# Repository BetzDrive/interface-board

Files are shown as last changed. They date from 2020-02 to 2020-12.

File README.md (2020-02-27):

# Interface Board

This board is intended to connect a chain of 48 VDC RS-485 motor controllers to
the outside world.

## Features

 * USB - RS485 conversion. This is accomplished via the [FT232H](https://www.ftdichip.com/Products/ICs/FT232H.htm) and [ADM2682E](https://www.analog.com/en/products/adm2682e.html)
 IC's. The combination of these chips should provide full electrical isolation
 to the USB host and allow ~10 Mbps throughput to/from RS485.

 * Input power sanitizing. A [LM5066](https://www.ti.com/product/LM5066)
 hotswap controller IC provides sane controlled voltage ramps when the device
 is hot-plugged, and cuts power to the system when it exceeds ~56 volts. An
 input TVS diode starts kicks in around 65 V.

 * Backdrive surge supressing. Sometimes when motors are aggressively
 backdriven by an external power source, significant voltages are generated
 "back" onto the motor bus. The board is equipped to detect this condition and
 dump power through a 10-ohm power resistor. Hysteresis and timing is provided
 by a STM32L071 microcontroller.

## Resources

 * [Schematics in PDF](hardware/blue_interface_board.pdf)
 * KiCAD design files are found in [`hardware`](hardware)
 * fabrication files for rev.A are found in [`hardware/fab`](hardware/fab)

## Renderings

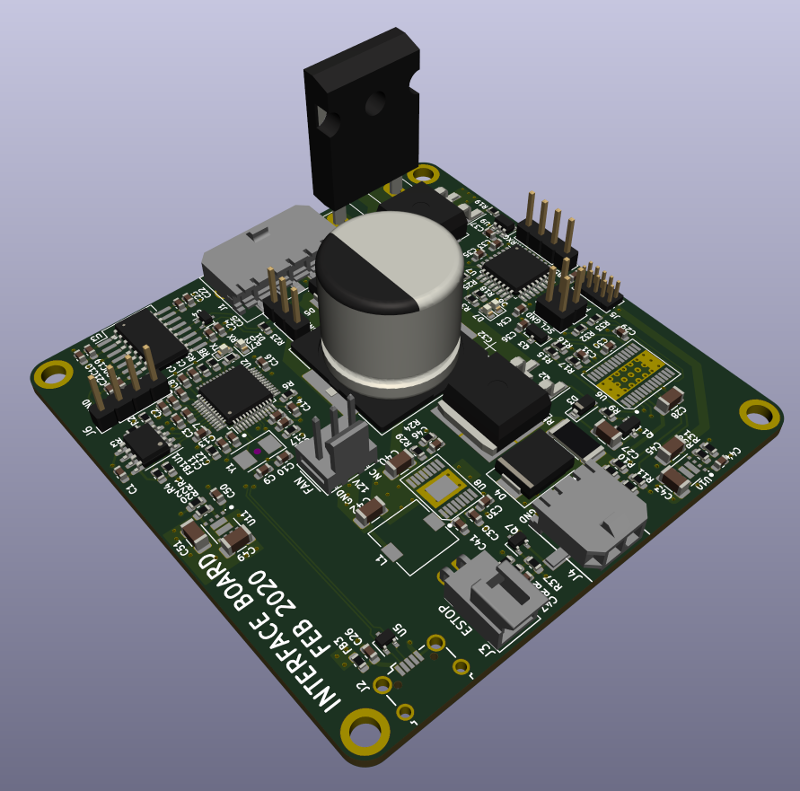
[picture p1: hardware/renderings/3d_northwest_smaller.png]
3d Northwest

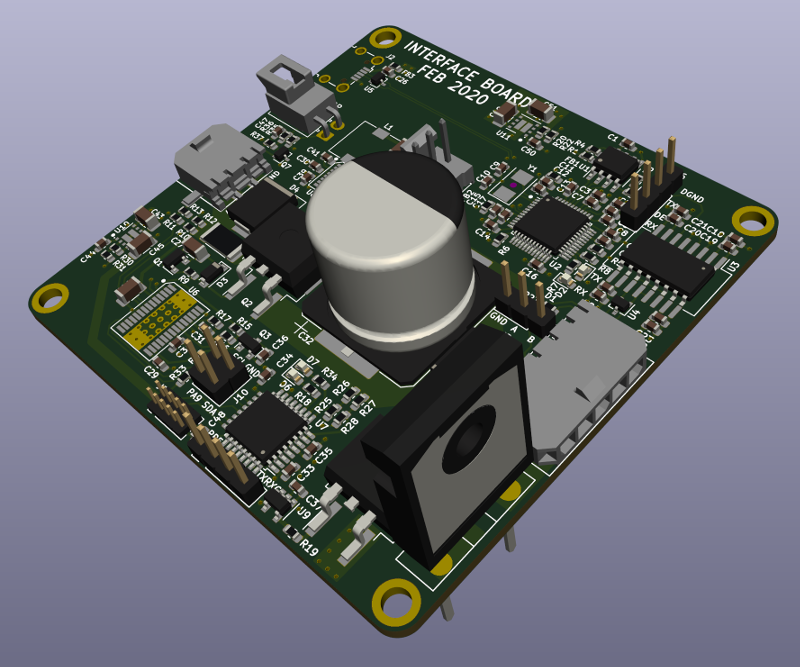
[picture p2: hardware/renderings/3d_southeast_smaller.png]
3d Southeast

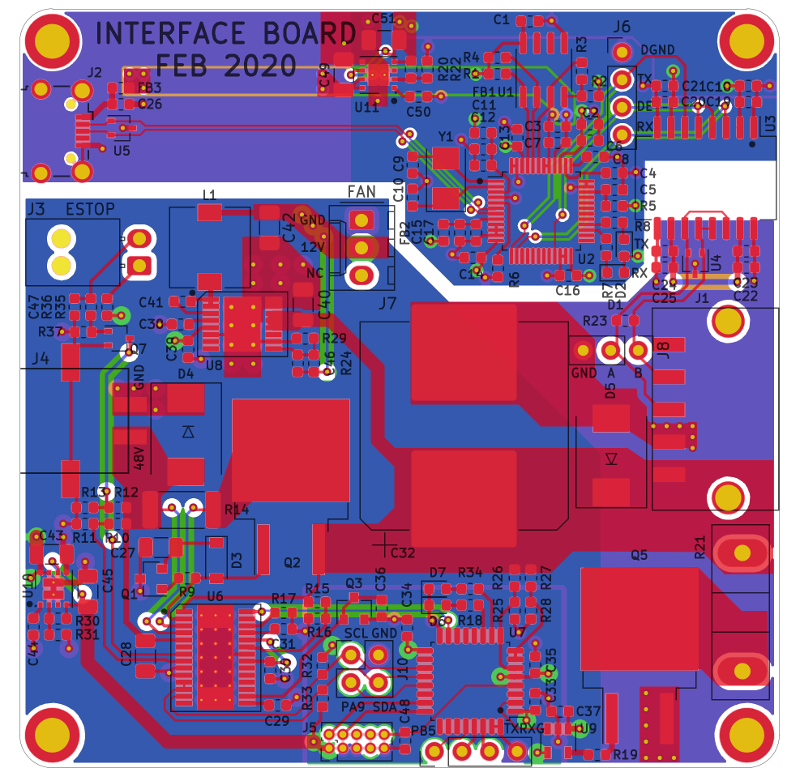
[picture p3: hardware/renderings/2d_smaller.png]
2d


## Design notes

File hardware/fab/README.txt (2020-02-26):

PCB fabrication notes
====
 * 4 layers
 * rectangular, 70mm x 70mm
 * 1.6mm finished thickness
 * green soldermask
 * white silkscreen
 * minimum via size 0.76mm (30mil), minimum via drill 0.38mm (15mil)
 * minimum trace/space 0.178mm (7mil)

Assembly notes:
====
 * SMT top side only. Minimum passives 0603.
 * two DFN regulator modules
 * otherwise, all legged IC packages: QFP, TSSOP, SOIC, etc.
 * please ignore all parts with "Do Not Populate" (DNP) part numbers
 * one through-hole power resistor (vertical TO-247 style)
 * three through-hole connectors
 * other through-hole connectors are DNP

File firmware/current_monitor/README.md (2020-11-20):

# compile it

```
git submodule init
git submodule update
sudo apt install gcc-arm-none-eabi
make
```

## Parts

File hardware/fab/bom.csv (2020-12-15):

Component | Quantity Per PCB | References | Value | Footprint | MFN | MPN | D1N | D1PN | Maximum Voltage | Tolerance
1 | 19 | C1 C4 C6 C7 C8 C12 C13 C14 C16 C17 C18 C20 C22 C24 C33 C34 C35 C47 C48 | 100n | C_0603_1608Metric | Yageo | CC0603KRX7R9BB104 | Digikey | 311-1344-1-ND
2 | 1 | C28 | 100nF | C_1206_3216Metric | AVX | 12061C104KAT2A | Digikey | 478-1529-1-ND | 100 V | 10%
3 | 4 | C5 C19 C23 C26 | 10n | C_0603_1608Metric | Yageo | CC0603KPX7R9BB103 | Digikey | 311-1572-1-ND
4 | 2 | C21 C25 | 10u | C_0603_1608Metric | Murata | GRM188R61A106KE69J | Digikey | 490-14372-1-ND
5 | 1 | C27 | 150nF | C_1206_3216Metric | KEMET | C1206C154KARACAUTO | Digikey | 399-17949-1-ND | 250 V | 10%
6 | 1 | C36 | 1n | C_0603_1608Metric | Yageo | CC0603KRX7R9BB102 | Digikey | 311-1080-1-ND
7 | 4 | C29 C30 C37 C39 | 1u | C_0603_1608Metric | Yageo | CC0603KRX5R8BB105 | Digikey | 311-1445-1-ND
8 | 3 | C42 C43 C49 | 22u | C_1206_3216Metric | Samsung | CL31A226KAHNNNE | Digikey | 1276-3047-1-ND | 25 V | 10%
9 | 2 | C9 C10 | 27p | C_0603_1608Metric | Yageo | CC0603JRNPO9BN270 | Digikey | 311-1063-1-ND
10 | 1 | C38 | 2u2 | C_0603_1608Metric | Yageo | CC0603KRX5R6BB225 | Digikey | 311-1451-1-ND | 10 V | 10%
11 | 4 | C2 C3 C11 C15 | 4.7u | C_0603_1608Metric | Tayio Yuden | LMK107BJ475KA-T | Digikey | 587-1441-1-ND | 10 V | 10%
12 | 1 | C41 | 470n | C_0603_1608Metric | Yageo | CC0603KRX5R8BB474 | Digikey | 311-3365-1-ND | 25 V | 10%
13 | 1 | C32 | 470u | CP_Elec_18x17.5 | Panasonic | EEE-FK1K471AM | Digikey | PCE4859CT-ND | 80 V | 20%
14 | 1 | C31 | 47n | C_0603_1608Metric | Samsung Electro-Mechanics | CL10B473JB8NNNC | Digikey | 1276-2070-2-ND
15 | 2 | C45 C51 | 47u | C_1206_3216Metric | Murata | GRM31CR61A476ME15L | Digikey | 490-5528-1-ND | 10 V | 10%
16 | 2 | C44 C50 | 4n7 | C_0603_1608Metric | Yageo | CC0603KRX7R0BB472 | Digikey | 311-3366-1-ND | 25 V | 10%
17 | 1 | C40 | 4u7 | C_1206_3216Metric | Murata | GRM31CC72A475KE11L | Digikey | 490-18620-1-ND | 100 V | 10%
18 | 1 | C46 | 82p | C_0603_1608Metric | Samsung | CL10C820JC81PNC | Digikey | 1276-2344-1-ND | 100 V | 5%
19 | 1 | D3 | 1N4148W-7-F | D_SOD-123 | Diodes Inc | 1N4148W-7-F | Digikey | 1N4148W-FDICT-ND
20 | 1 | D4 | 5.0SMDJ60A | D_SMC | Bourns | 5.0SMDJ60A | Digikey | 5.0SMDJ60ABBCT-ND
21 | 1 | D5 | B380-13-F | D_SMC | Diodes Inc | B380-13-F | Digikey | B380-FDICT-ND
22 | 2 | D1 D7 | GREEN | LED_0603_1608Metric | Wurth | 150060VS75000 | Digikey | 732-4980-1-ND
23 | 2 | D2 D6 | RED | LED_0603_1608Metric | Wurth | 150060RS75000 | Digikey | 732-4978-1-ND
24 | 3 | FB1 FB2 FB3 | 600R | R_0603_1608Metric | Wurth | 742792651 | Digikey | 732-1593-1-ND
25 | 1 | J5 | Conn_ARM_JTAG_SWD_10 | PinHeader_2x05_P1.27mm_Vertical | Sullins | GRPB052VWVN-RC | Digikey | S9015E-05-ND
26 | 1 | J3 | ESTOP | Molex_Nano-Fit_105313-xx02_1x02_P2.50mm_Horizontal | Molex | 1053131302 | Digikey | WM15141-ND
27 | 1 | J7 | FAN | Molex_KK-254_AE-6410-03A_1x03_P2.54mm_Vertical | Molex | 22232031 | Digikey | WM4201-ND
28 | 1 | J10 | I2C | PinHeader_2x02_P2.54mm_Vertical | DNP | DNP | DNP | DNP
29 | 1 | J4 | PWR | molex-0436500213 | Molex | 436500214 | Digikey | WM14310CT-ND
30 | 1 | J2 | USB_B_Micro | USB_Micro-B_Wuerth_629105150521_CircularHoles | Wurth | 629105150521 | Digikey | 732-5960-6-ND
31 | 1 | J1 | arm connector | molex-436500511 | Molex | 436500510 | Digikey | WM1888CT-ND
32 | 2 | J6 J9 | logic-side RS485 debug/expansion | PinHeader_1x04_P2.54mm_Vertical | DNP | DNP | DNP | DNP
33 | 1 | J8 | power-side RS485 debug/expansion | PinHeader_1x03_P2.54mm_Vertical | DNP | DNP | DNP | DNP
34 | 1 | L1 | 100u | L_7.3x7.3_H4.5 | Wurth | 744777920 | Digikey | 732-1199
35 | 1 | Q3 | MMBT3904 | SOT-23 | Diodes Inc | MMBT3904-7-F | Digikey | MMBT3904-FDICT-ND
36 | 1 | Q1 | MMBT5401LT1G | SOT-23 | ON Semi | MMBT5401LT1G | Digikey | MMBT5401LT1GOSCT-ND
37 | 1 | Q7 | NTS4001NT1G | SOT-323_SC-70 | ON Semi | NTS4001NT1G | Digikey | NTS4001NT1GOSTR-ND
38 | 2 | Q2 Q5 | PSMN4R8-100BSEJ | TO-263-2 | NXP | PSMN4R8-100BSEJ | Digikey | 1727-1103-1-ND
39 | 1 | R37 | 100k | R_0603_1608Metric | Yageo | RC0603FR-07100KL | Digikey | 311-100KHRCT-ND |  | 1%
40 | 5 | R1 R2 R4 R5 R36 | 10K | R_0603_1608Metric | Yageo | RC0603JR-0710KL | Digikey | 311-10KGRCT-ND
41 | 1 | R21 | 10R | TO-247-2_Vertical | Riedon | PF2472-10RF1 | Digikey | 696-1107-5-ND
42 | 1 | R23 | 120 | R_0603_1608Metric | Yageo | RC0603FR-07120RL | Digikey | 311-120HRCT-ND |  | 1%
43 | 1 | R6 | 12K | R_0603_1608Metric | Panasonic | ERA-3AEB123V | Digikey | P12KDBCT-ND |  | 0.1%
44 | 1 | R16 | 13.3k | R_0603_1608Metric | Panasonic | ERA-3AEB1332V | Digikey | P13.3KDBTR-ND |  | 0.1%
45 | 6 | R10 R12 R22 R26 R27 R31 | 140k | R_0603_1608Metric | Panasonic | ERA-3AEB1403V | Digikey | P140KDBCT-ND |  | 0.1%
46 | 1 | R24 | 1M | R_0603_1608Metric | Yageo | RC0603FR-071ML | Digikey | 311-1.00MHRCT-ND |  | 1%
47 | 2 | R9 R35 | 1k | R_0603_1608Metric | Yageo | RC0603FR-071KL | Digikey | 311-1.00KHRCT-ND |  | 1%
48 | 3 | R3 R32 R33 | 2.2k | R_0603_1608Metric | Yageo | RC0603FR-072K2L | Digikey | 311-2.20KHRCT-ND |  | 1%
49 | 1 | R15 | 240k | R_0603_1608Metric | Panasonic | ERA-3AEB244V | Digikey | P240KDBTR-ND |  | 0.1%
50 | 1 | R13 | 25k5 | R_0603_1608Metric | Panasonic | ERA-3AEB2552V | Digikey | P25.5KDBCT-ND |  | 0.1%
51 | 1 | R17 | 300k | R_0603_1608Metric | Panasonic | ERA-3AEB304V | Digikey | P300KDBTR-ND |  | 0.1%
52 | 1 | R19 | 33 | R_0603_1608Metric | Yageo | RC0603FR-0733RL | Digikey | 311-33.0HRCT-ND |  | 1%
53 | 2 | R20 R30 | 437k | R_0603_1608Metric | Yageo | RC0603FR-07432KL | Digikey | 311-432KHRCT-ND |  | 1%
54 | 4 | R7 R8 R18 R34 | 470R | R_0603_1608Metric | Yageo | RC0603FR-07470RL | Digikey | 311-470HRCT-ND |  | 1%
55 | 1 | R14 | 4m | R_2512_6332Metric | Vishay Dale | WSL25124L000FEA18 | Digikey | WSLH-.004TR-ND
56 | 1 | R28 | 6.34k | R_0603_1608Metric | Panasonic | ERA-3AEB6341V | Digikey | P6.34KDBCT-ND |  | 0.1%
57 | 1 | R25 | 6.65k | R_0603_1608Metric | Panasonic | ERA-3AEB6651V | Digikey | P6.65KDBCT-ND |  | 0.1%
58 | 1 | R11 | 6k49 | R_0603_1608Metric | Panasonic | ERA-3AEB6491V | Digikey | P6.49KDBCT-ND |  | 0.1%
59 | 1 | R29 | 91k | R_0603_1608Metric | Yageo | RC0603FR-0791KL | Digikey | 311-91.0KHRDKR-ND |  | 1%
60 | 1 | U1 | 93LCxxB | SOIC-8_3.9x4.9mm_P1.27mm | Microchip | 93LC56B/SN | Digikey | 93LC56B/SN-ND
61 | 1 | U3 | ADM2682E | SOIC-16W_7.5x12.8mm_P1.27mm | Analog Devices | ADM2682EBRIZ | Digikey | ADM2682EBRIZ-ND
62 | 1 | U9 | FAN3111E | SOT-23-5 | ON Semi | FAN3111ESX | Digikey | FAN3111ESXCT-ND
63 | 1 | U2 | FT232H | LQFP-48_7x7mm_P0.5mm | FTDI | FT232HL-REEL | Digikey | 768-1101-1-ND
64 | 1 | U8 | LM46000 | PWP0016G | TI | LM46000PWPR | Digikey | 296-40222-1-ND
65 | 1 | U6 | LM5066 | Texas_PWP0028A | TI | LM5066PMHX/NOPB | Digikey | 296-LM5066PMHX/NOPBCT-ND
66 | 2 | U10 U11 | LMZ21700SIL | SIL0008E | TI | LMZ21700SILR | Digikey | 296-44325-1-ND
67 | 1 | U7 | STM32L071KZT6 | LQFP-32_7x7mm_P0.8mm | ST | STM32L071KZT6 | Digikey | 497-18578-ND
68 | 2 | U4 U5 | TPD2E2U06DCK | SOT-323_SC-70 | TI | TPD2E2U06DCKR | Digikey | 296-TPD2E2U06DCKRDKR-ND
69 | 1 | Y1 | 12MHz | Crystal_SMD_5032-2Pin_5.0x3.2mm | Kyocera | CX5032GB12000H0HPQZ1 | Digikey | 1253-1375-1-ND
Component Groups: | 69
Component Count: | 126
Fitted Components: | 126
Number of PCBs: | 1
Total components: | 126
Schematic Version:
Schematic Date:
PCB Variant: | ['default']
BoM Date: | Mon 14 Dec 2020 11:55:06 PM PST
Schematic Source: | blue_interface_board.kicad_sch
KiCad Version: | Eeschema 5.99.0-unknown-dd374e12a~102~ubuntu20.04.1

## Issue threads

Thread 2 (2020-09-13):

Firmware for Reverse Current Circuitry

gbalke, 2020-09-13:
A small driver needs to be written to toggle the shunt (R21) in case of regeneration caused by backdrive of the motor controllers. For now, R21 is to be left unpopulated.

gbalke, 2020-11-11:
Initial steps addressed by #4.

gbalke, 2020-11-19:
Currently debugging upload issues on this [branch](https://github.com/BetzDrive/interface-board/tree/upload_debug) with firmware [here](https://github.com/BetzDrive/interface-board/tree/upload_debug/firmware/current_monitor).

When I upload and attach a debugger I get the following:
```
Reading symbols from build/program.elf...
Remote debugging using localhost:3333
0xbc08bcf8 in ?? ()
(gdb) b *main
Breakpoint 1 at 0x8130: file src/main.c, line 18.
(gdb) start
The program being debugged has been started already.
Start it from the beginning? (y or n) y
Temporary breakpoint 2 at 0x8134: file src/main.c, line 21.
Starting program: ......./project/build/program.elf
Note: automatically using hardware breakpoints for read-only addresses.
^C
Program received signal SIGTRAP, Trace/breakpoint trap.
0xfffffffe in ?? ()
(gdb)
```

Probing shows everything is working alright...
```
$ st-info --probe
Found 1 stlink programmers
 serial: 303030303030303030303031
openocd: "\x30\x30\x30\x30\x30\x30\x30\x30\x30\x30\x30\x31"
  flash: 196608 (pagesize: 128)
   sram: 20480
 chipid: 0x0447
  descr: L0x Category 5 device
```

My openocd upload is definitely complaining but not failing and I've had similar results using st-flash:
```
Info : Device: STM32L0xx (Cat.5)
Info : STM32L flash has dual banks. Bank (0) size is 128kb, base address is 0x8000000
flash 'stm32lx' found at 0x08000000
auto erase enabled
Warn : couldn't use loader, falling back to page memory writes
wrote 8192 bytes from file build/program.bin in 1.138968s (7.024 KiB/s)
Error: JTAG failure
Error: Error setting register
Error: timed out while waiting for target halted
target halted due to debug-request, current mode: Handler HardFault
xPSR: 0xf0000003 pc: 0xfffffffe msp: 0x46c0b5f8
Error: error executing cortex_m crc algorithm
verified 6784 bytes in 20.159586s (0.329 KiB/s)
adapter speed: 300 kHz
shutdown command invoked
```

The crc error comes and goes...

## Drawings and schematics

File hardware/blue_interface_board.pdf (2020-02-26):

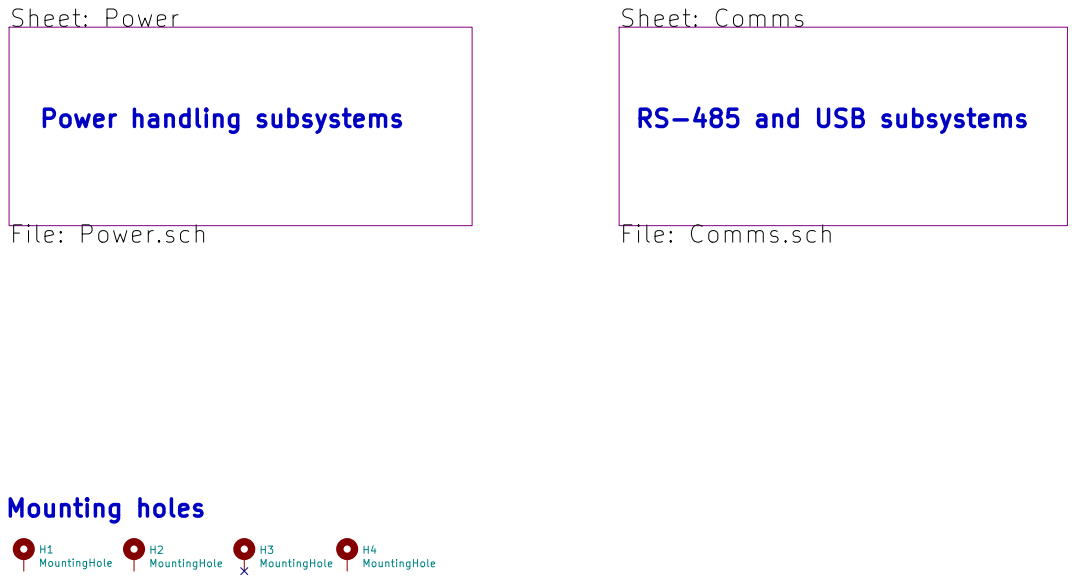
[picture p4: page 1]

File: blue_interface_board.sch Sheet: / Sheet: Comms

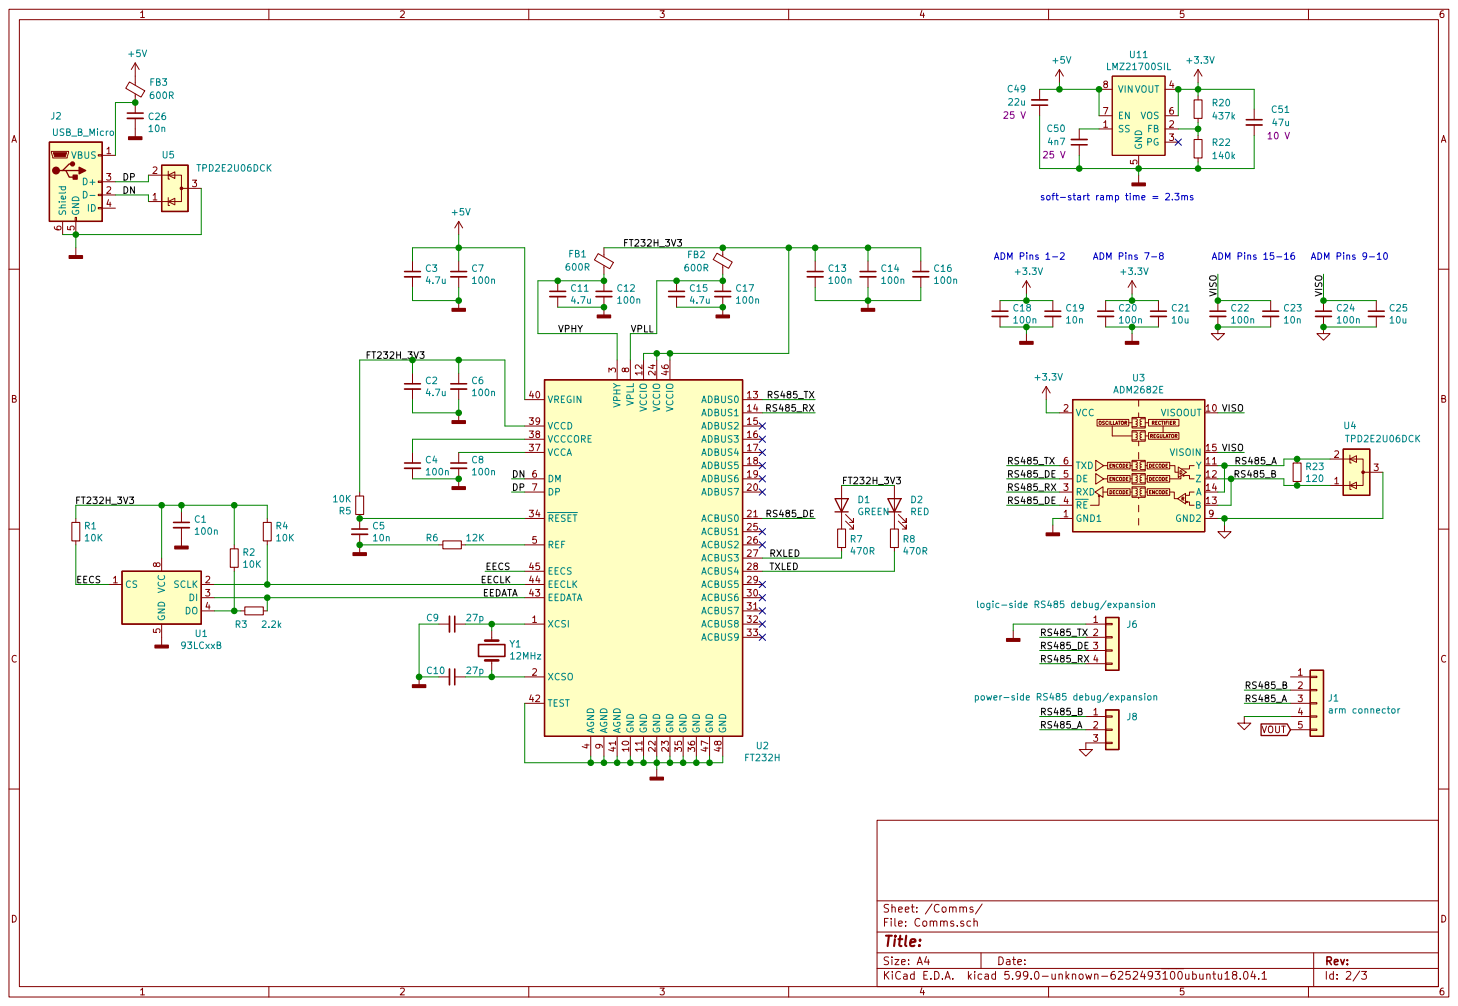
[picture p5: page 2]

5 VOS 6 EN 7 VIN 8 SS 1 U11

soft-start ramp time = 2.3ms

4 VREGIN 40 AGND 41 TEST 42 EEDATA 43 EECLK 44 EECS 45 VCCIO 46 GND 47 GND 48 REF 5 DM 6 DP 7 VPLL

3 ACBUS6 30 ACBUS7 31 ACBUS8 32 ACBUS9 33 RESET 34 GND 35 GND 36 VCCA 37 VCCCORE 38 VCCD 39 AGND

Id: 2/3 Title: File: Comms.sch Sheet: /Comms/ R5

power-side RS485 debug/expansion

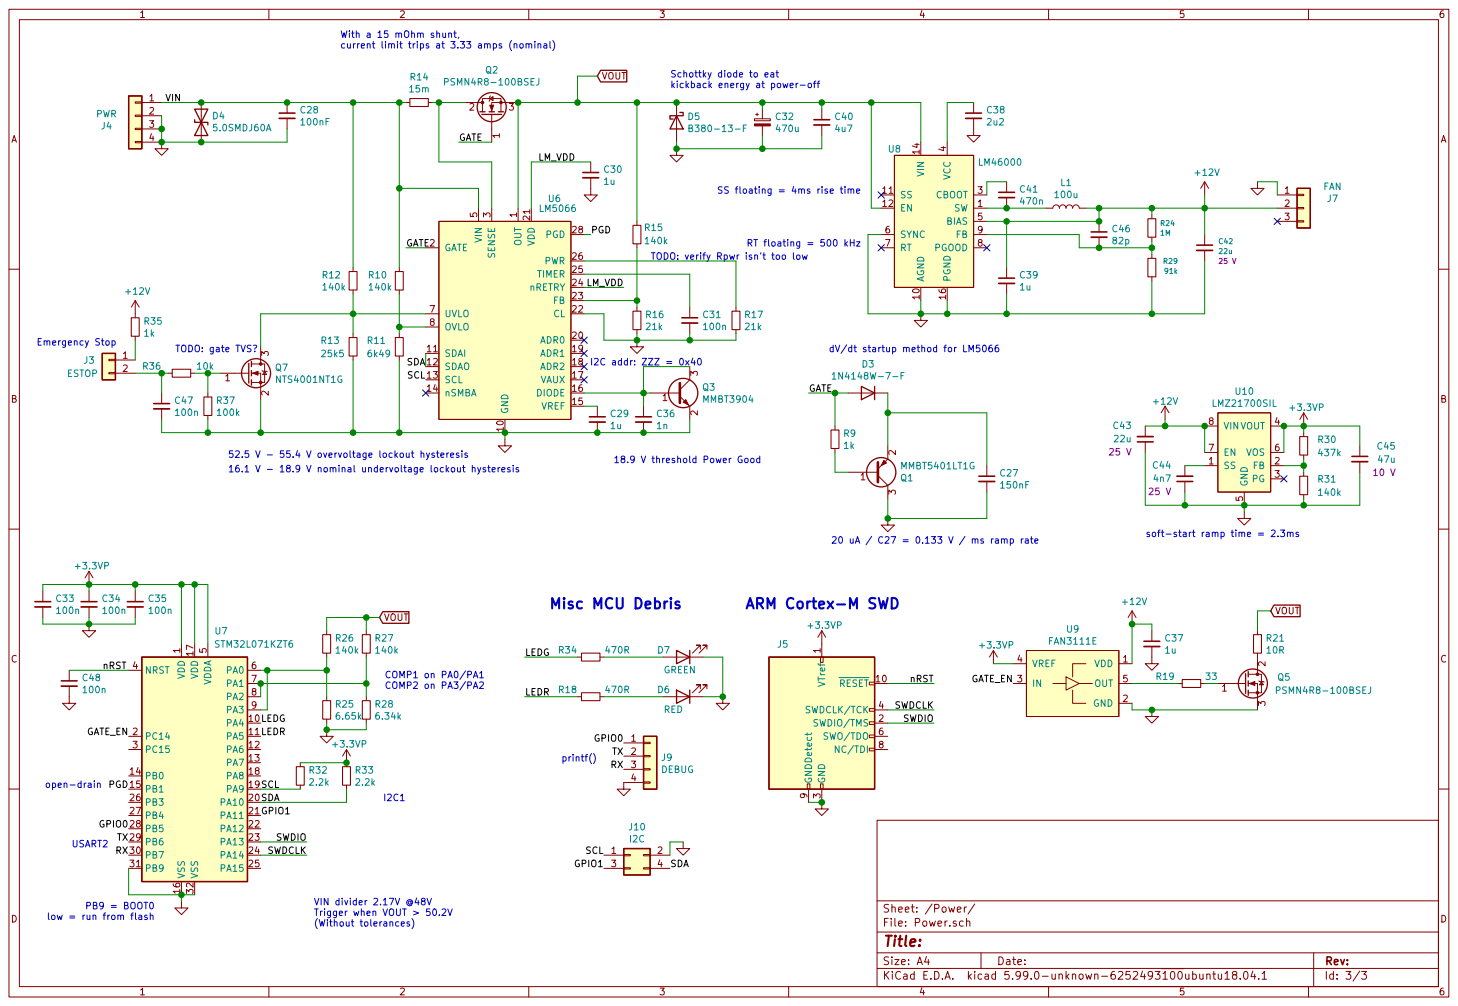
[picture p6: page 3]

With a 15 mOhm shunt, current limit trips at 3.33 amps (nominal)
VOUT VOUT SWDCLK

Schottky diode to eat
kickback energy at power-off

4 BIAS 5 SYNC 6 RT 7 PGOOD 8 FB 9 U8

SS floating = 4ms rise time

1 GND 10 SDAI 11 SDAO 12 SCL 13
GATE

TODO: verify Rpwr isn't too low

5 VOS 6 EN 7 VIN 8 SS 1 U10
LMZ21700SIL

18.9 V threshold Power Good VIN divider 2.17V @48V

2 3 Q1MMBT5401LT1G VTref 1 RESET 10 SWDIO/TMS 2 GND

16.1 V - 18.9 V nominal undervoltage lockout hysteresis

20 uA / C27 = 0.133 V / ms ramp rate COMP1 on PA0/PA1 COMP2 on PA3/PA2

soft-start ramp time = 2.3ms

3 SWDCLK/TCK 4 SWO/TDO 6 NC/TDI 8 GNDDetect 9

low = run from flash

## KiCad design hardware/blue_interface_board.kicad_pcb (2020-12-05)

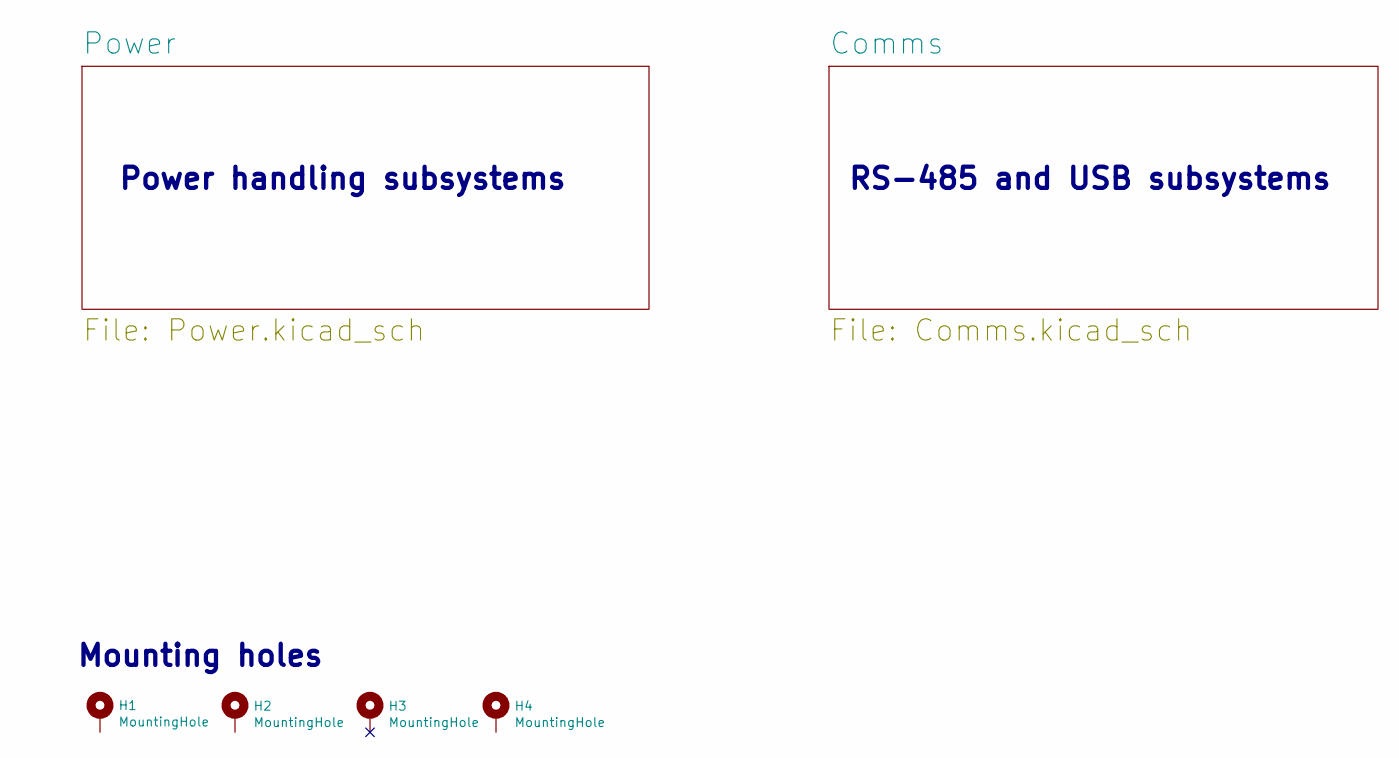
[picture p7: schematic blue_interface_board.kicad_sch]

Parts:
H1, H2, H3, H4: MountingHole; MountingHole_3.2mm_M3_DIN965_Pad

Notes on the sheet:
Mounting holes
Power handling subsystems
RS-485 and USB subsystems

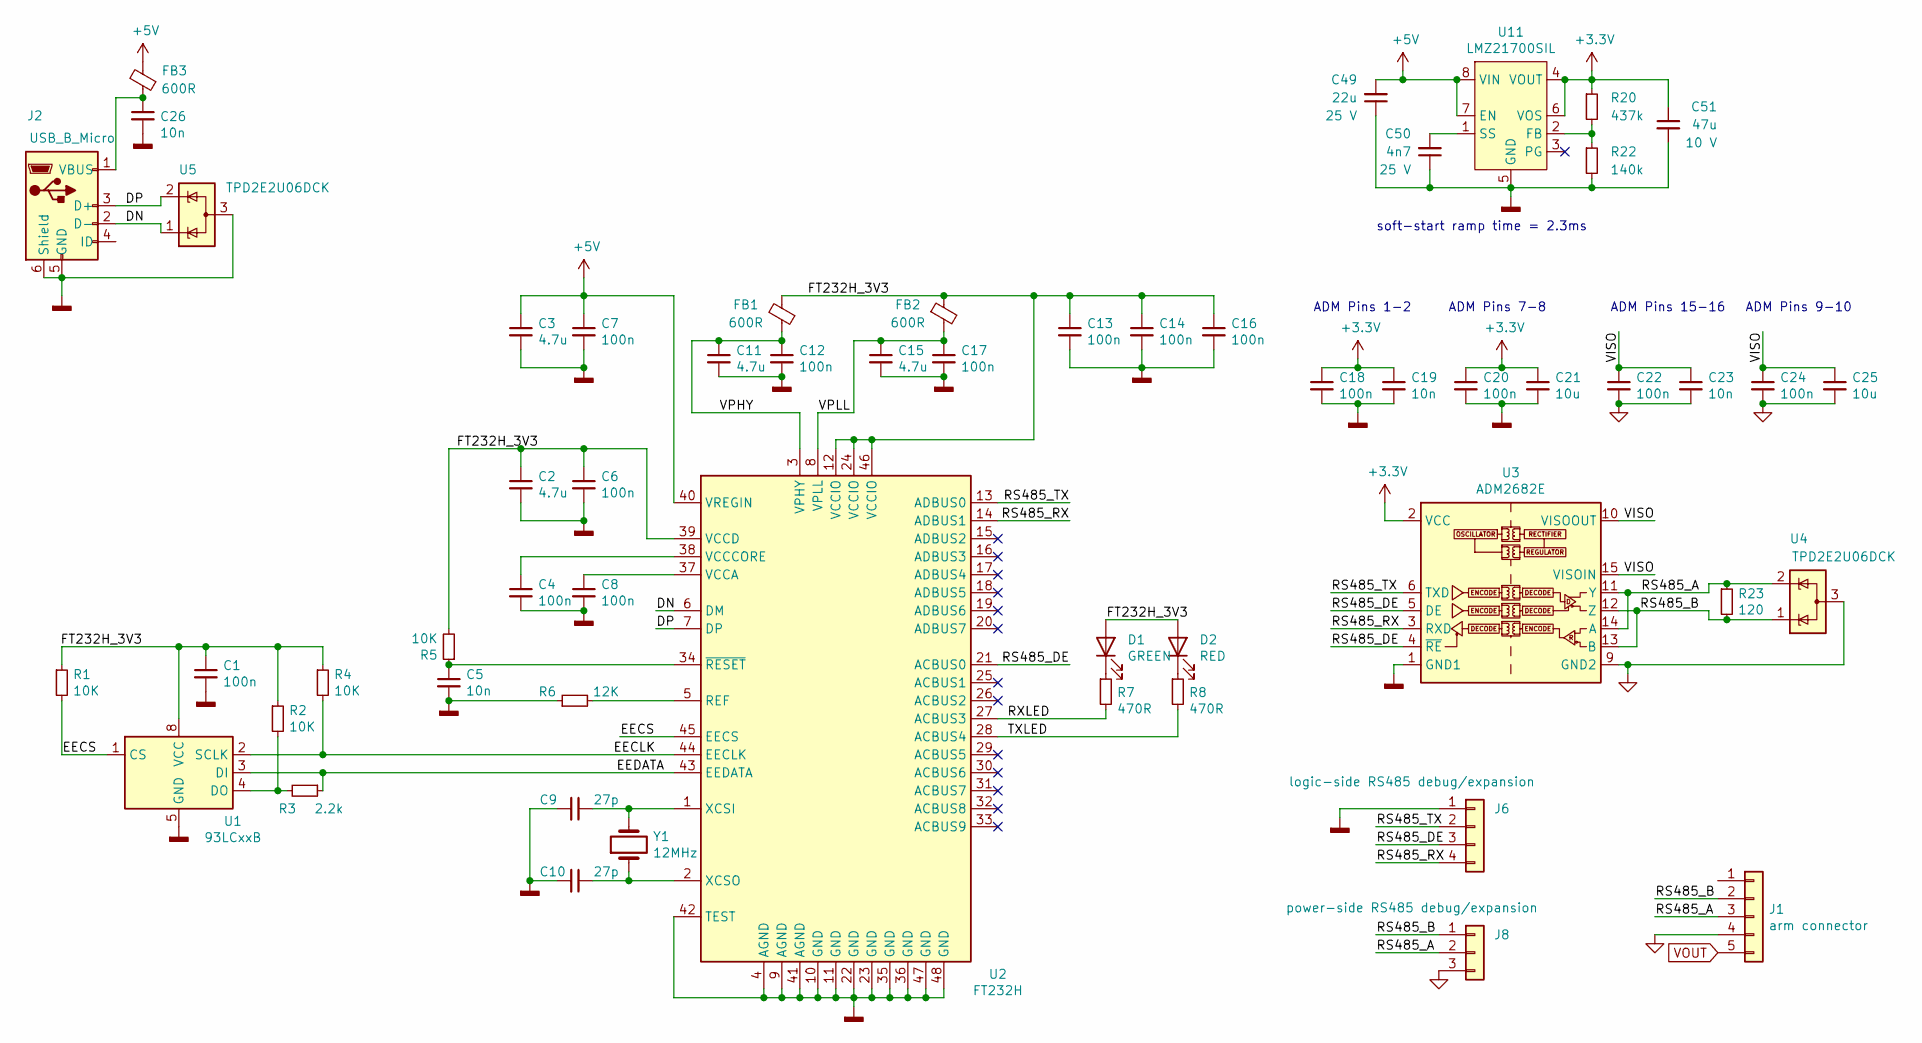
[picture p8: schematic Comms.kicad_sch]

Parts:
C1, C4, C6, C7, C8, C12, C13, C14, C16, C17, C18, C20, C22, C24: 100n; C_0603_1608Metric; MPN CC0603KRX7R9BB104
C2, C3, C11, C15: 4.7u; C_0603_1608Metric; Maximum Voltage 10 V; Tolerance 10%; MPN LMK107BJ475KA-T
C5, C19, C23, C26: 10n; C_0603_1608Metric; MPN CC0603KPX7R9BB103
C9, C10: 27p; C_0603_1608Metric; MPN CC0603JRNPO9BN270
C21, C25: 10u; C_0603_1608Metric; MPN GRM188R61A106KE69J
C49: 22u; C_1206_3216Metric; Maximum Voltage 25 V; Tolerance 10%; MPN CL31A226KAHNNNE
C50: 4n7; C_0603_1608Metric; Maximum Voltage 25 V; Tolerance 10%; MPN CC0603KRX7R0BB472
C51: 47u; C_1206_3216Metric; Maximum Voltage 10 V; Tolerance 10%; MPN GRM31CR61A476ME15L
D1: GREEN; LED_0603_1608Metric; MPN 150060VS75000
D2: RED; LED_0603_1608Metric; MPN 150060RS75000
FB1, FB2, FB3: 600R; R_0603_1608Metric; MPN 742792651
J1: arm connector; molex-436500511; MPN 436500510
J2: USB_B_Micro; USB_Micro-B_Wuerth_629105150521_CircularHoles; MPN 629105150521
J6: logic-side RS485 debug/expansion; PinHeader_1x04_P2.54mm_Vertical; MPN DNP
J8: power-side RS485 debug/expansion; PinHeader_1x03_P2.54mm_Vertical; MPN DNP
R1, R2, R4, R5: 10K; R_0603_1608Metric; MPN RC0603JR-0710KL
R3: 2.2k; R_0603_1608Metric; Tolerance 1%; MPN RC0603FR-072K2L
R6: 12K; R_0603_1608Metric; Tolerance 0.1%; MPN ERA-3AEB123V
R7, R8: 470R; R_0603_1608Metric; Tolerance 1%; MPN RC0603FR-07470RL
R20: 437k; R_0603_1608Metric; Tolerance 1%; MPN RC0603FR-07432KL
R22: 140k; R_0603_1608Metric; Tolerance 0.1%; MPN ERA-3AEB1403V
R23: 120; R_0603_1608Metric; Tolerance 1%; MPN RC0603FR-07120RL
U1: 93LCxxB; SOIC-8_3.9x4.9mm_P1.27mm; MPN 93LC56B/SN
U2: FT232H; LQFP-48_7x7mm_P0.5mm; MPN FT232HL-REEL
U3: ADM2682E; SOIC-16W_7.5x12.8mm_P1.27mm; MPN ADM2682EBRIZ
U4, U5: TPD2E2U06DCK; SOT-323_SC-70; MPN TPD2E2U06DCKR
U11: LMZ21700SIL; SIL0008E; MPN LMZ21700SILR
Y1: 12MHz; Crystal_SMD_5032-2Pin_5.0x3.2mm; MPN CX5032GB12000H0HPQZ1

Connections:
+3V3: C18.1, C19.1, C20.1, C21.1, C51.1, R20.1, U3.2 (VCC), U3.7 (VCC), U11.4 (VOUT), U11.6 (VOS)
+5V: C3.1, C7.1, C49.2, FB3.2, U2.40 (VREGIN), U11.7 (EN), U11.8 (VIN)
/Comms/DN: J2.2 (D-), U2.6 (DM), U5.1 (K)
/Comms/DP: J2.3 (D+), U2.7 (DP), U5.2 (K)
/Comms/EECLK: R4.2, U1.2 (SCLK), U2.44 (EECLK)
/Comms/EECS: R1.2, U1.1 (CS), U2.45 (EECS)
/Comms/EEDATA: R3.1, U1.3 (DI), U2.43 (EEDATA)
/Comms/FT232H_3V3: C1.1, C2.1, C6.1, C13.1, C14.1, C16.1, D1.2 (A), D2.2 (A), FB1.2, FB2.1, R1.1, R2.1, R4.1, R5.2, U1.8 (VCC), U2.12 (VCCIO), U2.24 (VCCIO), U2.39 (VCCD), U2.46 (VCCIO)
/Comms/RS485_A: J1.3, J8.2, R23.1, U3.11 (Y), U3.14 (A), U4.2 (K)
/Comms/RS485_B: J1.2, J8.1, R23.2, U3.12 (Z), U3.13 (B), U4.1 (K)
/Comms/RS485_DE: J6.3, U2.21 (ACBUS0), U3.4 (~RE), U3.5 (DE)
/Comms/RS485_RX: J6.4, U2.14 (ADBUS1), U3.3 (RXD)
/Comms/RS485_TX: J6.2, U2.13 (ADBUS0), U3.6 (TXD)
/Comms/RXLED: R7.2, U2.27 (ACBUS3)
/Comms/TXLED: R8.2, U2.28 (ACBUS4)
/Comms/VISO: C22.1, C23.1, C24.1, C25.1, U3.10 (VISOOUT), U3.15 (VISOIN)
/Comms/VPHY: C11.1, C12.1, FB1.1, U2.3 (VPHY)
/Comms/VPLL: C15.1, C17.1, FB2.2, U2.8 (VPLL)
GND: C22.2, C23.2, C24.2, C25.2, J1.4, J8.3, U3.9 (GND2), U3.16 (GND2), U4.3 (A); also elsewhere on the board
GNDD: C1.2, C2.2, C3.2, C4.2, C5.2, C6.2, C7.2, C8.2, C9.2, C10.2, C11.2, C12.2, C13.2, C14.2, C15.2, C16.2, C17.2, C18.2, C19.2, C20.2, C21.2, C26.2, C49.1, C50.1, C51.2, J2.5 (GND), J2.6 (Shield), J6.1, R6.1, R22.2, U1.5 (GND), U2.4 (AGND), U2.9 (AGND), U2.10 (GND), U2.11 (GND), U2.22 (GND), U2.23 (GND), U2.35 (GND), U2.36 (GND), U2.41 (AGND), U2.42 (TEST), U2.47 (GND), U2.48 (GND), U3.1 (GND1), U3.8 (GND1), U5.3 (A), U11.5 (GND), U11.9 (PAD)
unnamed: C4.1, U2.38 (VCCCORE)
unnamed: C5.1, R5.1, U2.34 (~RESET)
unnamed: C8.1, U2.37 (VCCA)
unnamed: C9.1, U2.1 (XCSI), Y1.2
unnamed: C10.1, U2.2 (XCSO), Y1.1
unnamed: C26.1, FB3.1, J2.1 (VBUS)
unnamed: C50.2, U11.1 (SS)
unnamed: D1.1 (K), R7.1
unnamed: D2.1 (K), R8.1
unnamed: R2.2, R3.2, U1.4 (DO)
unnamed: R6.2, U2.5 (REF)
unnamed: R20.2, R22.1, U11.2 (FB)
VOUT: J1.5; also elsewhere on the board

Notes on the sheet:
ADM Pins 1-2
soft-start ramp time = 2.3ms
ADM Pins 7-8
ADM Pins 15-16
ADM Pins 9-10

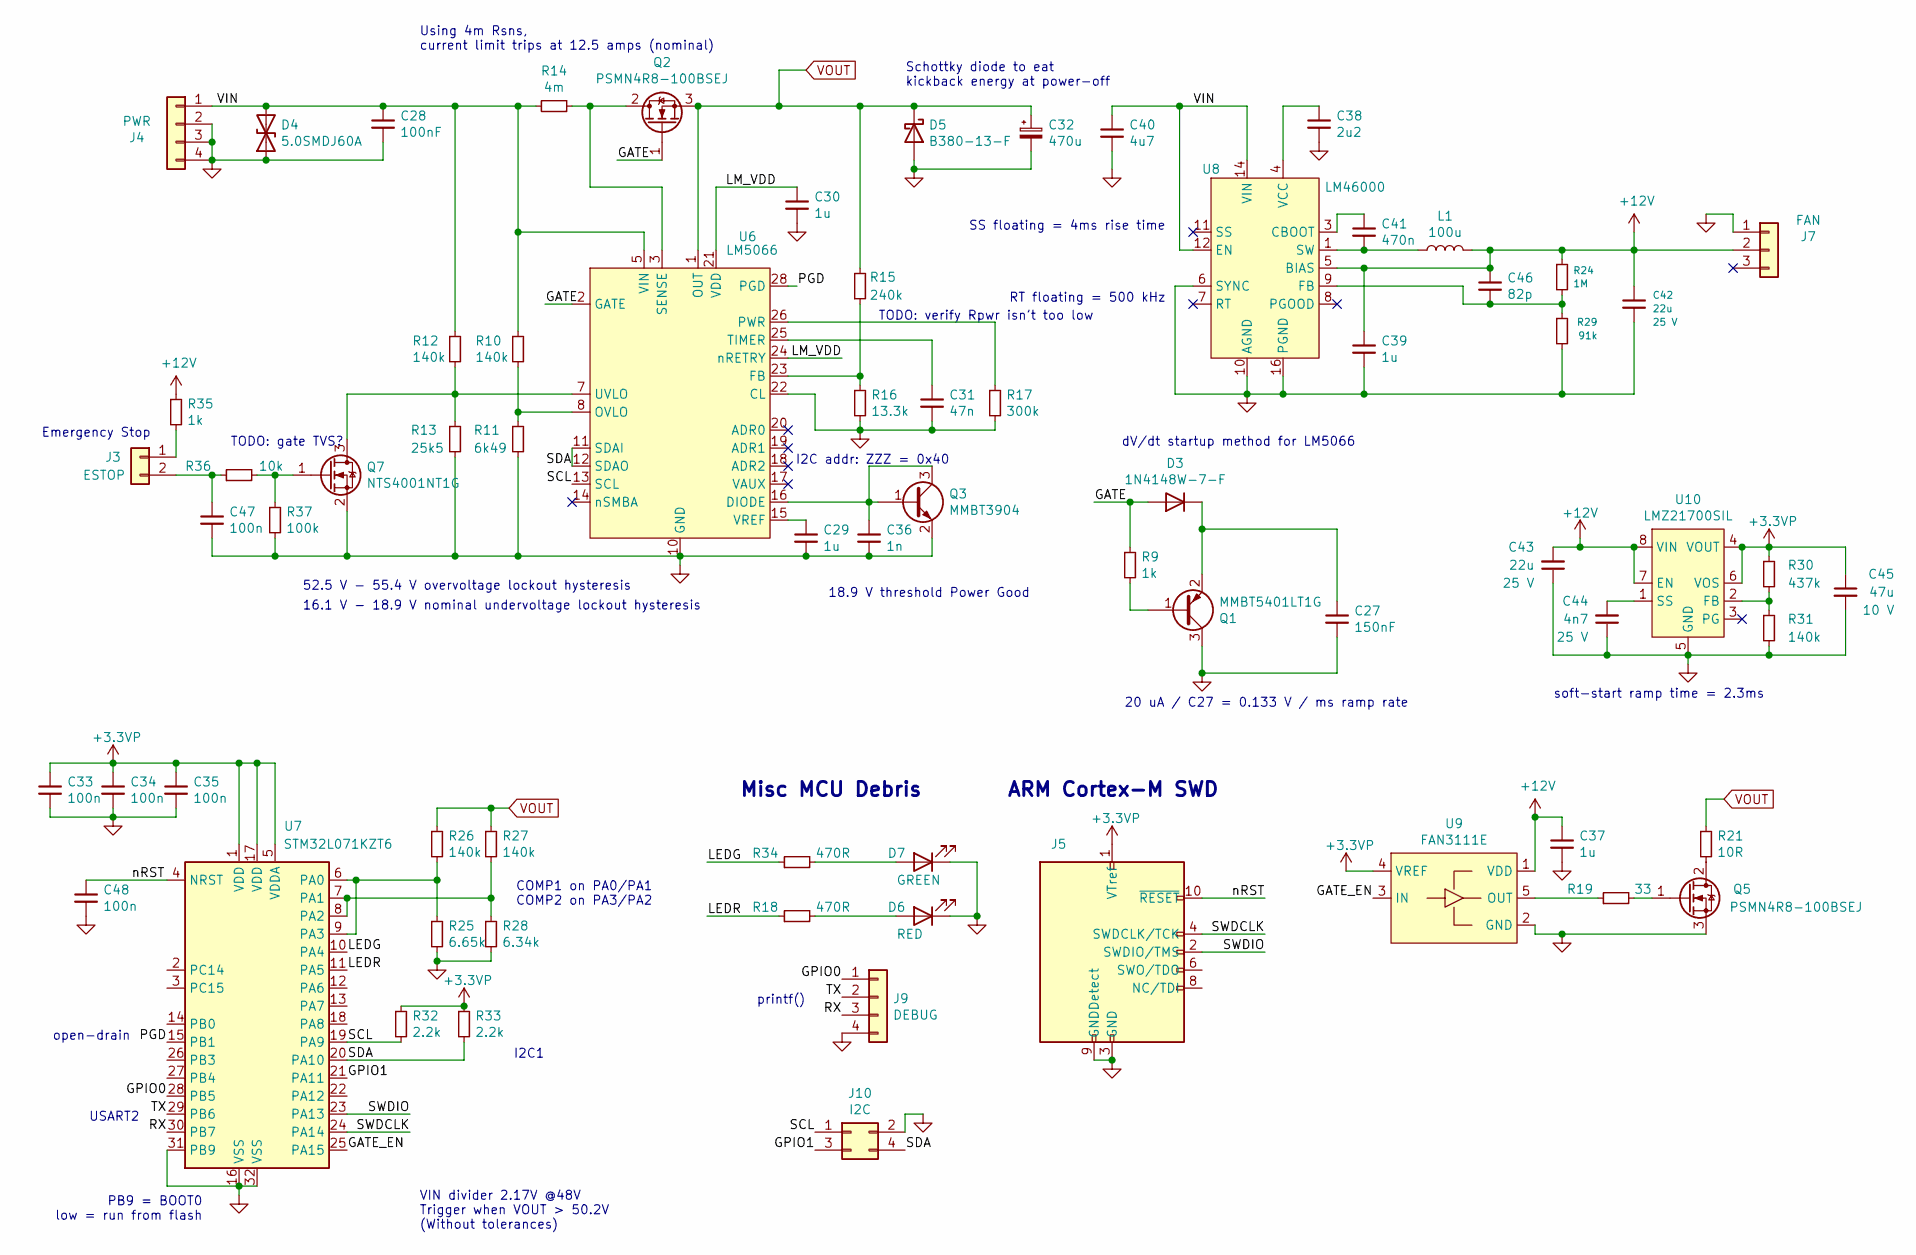
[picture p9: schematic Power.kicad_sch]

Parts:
C27: 150nF; C_1206_3216Metric; Maximum Voltage 250 V; Tolerance 10%; MPN C1206C154KARACAUTO
C28: 100nF; C_1206_3216Metric; Maximum Voltage 100 V; Tolerance 10%; MPN 12061C104KAT2A
C29, C30, C37, C39: 1u; C_0603_1608Metric; MPN CC0603KRX5R8BB105
C31: 47n; C_0603_1608Metric; MPN CL10B473JB8NNNC
C32: 470u; CP_Elec_18x17.5; Maximum Voltage 80 V; Tolerance 20%; MPN EEE-FK1K471AM
C33, C34, C35, C47, C48: 100n; C_0603_1608Metric; MPN CC0603KRX7R9BB104
C36: 1n; C_0603_1608Metric; MPN CC0603KRX7R9BB102
C38: 2u2; C_0603_1608Metric; Maximum Voltage 10 V; Tolerance 10%; MPN CC0603KRX5R6BB225
C40: 4u7; C_1206_3216Metric; Maximum Voltage 100 V; Tolerance 10%; MPN GRM31CC72A475KE11L
C41: 470n; C_0603_1608Metric; Maximum Voltage 25 V; Tolerance 10%; MPN CC0603KRX5R8BB474
C42, C43: 22u; C_1206_3216Metric; Maximum Voltage 25 V; Tolerance 10%; MPN CL31A226KAHNNNE
C44: 4n7; C_0603_1608Metric; Maximum Voltage 25 V; Tolerance 10%; MPN CC0603KRX7R0BB472
C45: 47u; C_1206_3216Metric; Maximum Voltage 10 V; Tolerance 10%; MPN GRM31CR61A476ME15L
C46: 82p; C_0603_1608Metric; Maximum Voltage 100 V; Tolerance 5%; MPN CL10C820JC81PNC
D3: 1N4148W-7-F; D_SOD-123; MPN 1N4148W-7-F
D4: 5.0SMDJ60A; D_SMC; MPN 5.0SMDJ60A
D5: B380-13-F; D_SMC; MPN B380-13-F
D6: RED; LED_0603_1608Metric; MPN 150060RS75000
D7: GREEN; LED_0603_1608Metric; MPN 150060VS75000
J3: ESTOP; Molex_Nano-Fit_105313-xx02_1x02_P2.50mm_Horizontal; MPN 1053131302
J4: PWR; molex-0436500213; MPN 436500214
J5: Conn_ARM_JTAG_SWD_10; PinHeader_2x05_P1.27mm_Vertical; MPN GRPB052VWVN-RC
J7: FAN; Molex_KK-254_AE-6410-03A_1x03_P2.54mm_Vertical; MPN 22232031
J9: DEBUG; PinHeader_1x04_P2.54mm_Vertical; MPN DNP
J10: I2C; PinHeader_2x02_P2.54mm_Vertical; MPN DNP
L1: 100u; L_7.3x7.3_H4.5; MPN 744777920
Q1: MMBT5401LT1G; SOT-23; MPN MMBT5401LT1G
Q2, Q5: PSMN4R8-100BSEJ; TO-263-2; MPN PSMN4R8-100BSEJ
Q3: MMBT3904; SOT-23; MPN MMBT3904-7-F
Q7: NTS4001NT1G; SOT-323_SC-70; MPN NTS4001NT1G
R9, R35: 1k; R_0603_1608Metric; Tolerance 1%; MPN RC0603FR-071KL
R10, R12, R26, R27, R31: 140k; R_0603_1608Metric; Tolerance 0.1%; MPN ERA-3AEB1403V
R11: 6k49; R_0603_1608Metric; Tolerance 0.1%; MPN ERA-3AEB6491V
R13: 25k5; R_0603_1608Metric; Tolerance 0.1%; MPN ERA-3AEB2552V
R14: 4m; R_2512_6332Metric; MPN WSL25124L000FEA18
R15: 240k; R_0603_1608Metric; Tolerance 0.1%; MPN ERA-3AEB244V
R16: 13.3k; R_0603_1608Metric; Tolerance 0.1%; MPN ERA-3AEB1332V
R17: 300k; R_0603_1608Metric; Tolerance 0.1%; MPN ERA-3AEB304V
R18, R34: 470R; R_0603_1608Metric; Tolerance 1%; MPN RC0603FR-07470RL
R19: 33; R_0603_1608Metric; Tolerance 1%; MPN RC0603FR-0733RL
R21: 10R; TO-247-2_Vertical; MPN PF2472-10RF1
R24: 1M; R_0603_1608Metric; Tolerance 1%; MPN RC0603FR-071ML
R25: 6.65k; R_0603_1608Metric; Tolerance 0.1%; MPN ERA-3AEB6651V
R28: 6.34k; R_0603_1608Metric; Tolerance 0.1%; MPN ERA-3AEB6341V
R29: 91k; R_0603_1608Metric; Tolerance 1%; MPN RC0402FR-0791KL
R30: 437k; R_0603_1608Metric; Tolerance 1%; MPN RC0603FR-07432KL
R32, R33: 2.2k; R_0603_1608Metric; Tolerance 1%; MPN RC0603FR-072K2L
R36: 10k; R_0603_1608Metric; MPN RC0603JR-0710KL
R37: 100k; R_0603_1608Metric; Tolerance 1%; MPN RC0603FR-07100KL
U6: LM5066; Texas_PWP0028A; MPN LM5066PMHX/NOPB
U7: STM32L071KZT6; LQFP-32_7x7mm_P0.8mm; MPN STM32L071KZT6
U8: LM46000; PWP0016G; MPN LM46000PWPR
U9: FAN3111E; SOT-23-5; MPN FAN3111ESX
U10: LMZ21700SIL; SIL0008E; MPN LMZ21700SILR

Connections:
+3.3VP: C33.1, C34.1, C35.1, C45.1, J5.1 (VTref), R30.1, R32.1, R33.1, U7.1 (VDD), U7.5 (VDDA), U7.17 (VDD), U9.4 (VREF), U10.4 (VOUT), U10.6 (VOS)
+12V: C37.1, C39.1, C42.1, C43.2, C46.1, J7.2, L1.2, R24.1, R35.1, U8.5 (BIAS), U9.1 (VDD), U10.7 (EN), U10.8 (VIN)
/Power/GATE: D3.2 (A), Q2.1 (G), R9.1, U6.2 (GATE)
/Power/GATE_EN: U7.25 (PA15), U9.3 (IN)
/Power/GPIO0: J9.1, U7.28 (PB5)
/Power/GPIO1: J10.3, U7.21 (PA11)
/Power/LEDG: R34.1, U7.10 (PA4)
/Power/LEDR: R18.1, U7.11 (PA5)
/Power/LM_VDD: C30.1, U6.21 (VDD), U6.24 (nRETRY)
/Power/PGD: U6.28 (PGD), U7.15 (PB1)
/Power/RX: J9.3, U7.30 (PB7)
/Power/SCL: J10.1, R32.2, U6.13 (SCL), U7.19 (PA9)
/Power/SDA: J10.4, R33.2, U6.11 (SDAI), U6.12 (SDAO), U7.20 (PA10)
/Power/SWDCLK: J5.4 (SWDCLK/TCK), U7.24 (PA14)
/Power/SWDIO: J5.2 (SWDIO/TMS), U7.23 (PA13)
/Power/TX: J9.2, U7.29 (PB6)
/Power/VIN: C28.1, C40.1, D4.2 (A2), J4.1, R10.1, R12.1, R14.2, U6.4 (VIN_K), U6.5 (VIN), U8.12 (EN), U8.13 (VIN), U8.14 (VIN)
/Power/nRST: C48.1, J5.10 (~RESET~), U7.4 (NRST)
GND: C27.2, C28.2, C29.2, C30.2, C31.2, C32.2, C33.2, C34.2, C35.2, C36.2, C37.2, C38.2, C39.2, C40.2, C42.2, C43.1, C44.1, C45.2, C47.2, C48.2, D4.1 (A1), D5.2 (A), D6.1 (K), D7.1 (K), J4.2, J4.3, J4.4, J5.3 (GND), J5.5 (GND), J5.9 (GNDDetect), J7.1, J9.4, J10.2, Q1.3 (C), Q3.2 (E), Q5.3 (S), Q7.2 (S), R11.2, R13.2, R16.2, R17.2, R25.2, R28.2, R29.2, R31.2, R37.2, U6.9 (AGND), U6.10 (GND), U6.22 (CL), U6.29 (GND), U7.16 (VSS), U7.31 (PB9), U7.32 (VSS), U8.6 (SYNC), U8.10 (AGND), U8.15 (PGND), U8.16 (PGND), U8.17 (AGND), U9.2 (GND), U10.5 (GND), U10.9 (PAD); also elsewhere on the board
unnamed: C27.1, D3.1 (K), Q1.2 (E)
unnamed: C29.1, U6.15 (VREF)
unnamed: C31.1, U6.25 (TIMER)
unnamed: C36.1, Q3.1 (B), Q3.3 (C), U6.16 (DIODE)
unnamed: C38.1, U8.4 (VCC)
unnamed: C41.1, U8.3 (CBOOT)
unnamed: C41.2, L1.1, U8.1 (SW), U8.2 (SW)
unnamed: C44.2, U10.1 (SS)
unnamed: C46.2, R24.2, R29.1, U8.9 (FB)
unnamed: C47.1, J3.2, R36.1
unnamed: D6.2 (A), R18.2
unnamed: D7.2 (A), R34.2
unnamed: J3.1, R35.2
unnamed: Q1.1 (B), R9.2
unnamed: Q2.2 (D), R14.1, U6.3 (SENSE)
unnamed: Q5.1 (G), R19.2
unnamed: Q5.2 (D), R21.2
unnamed: Q7.1 (G), R36.2, R37.1
unnamed: Q7.3 (D), R12.2, R13.1, U6.7 (UVLO)
unnamed: R10.2, R11.1, U6.8 (OVLO)
unnamed: R15.1, R16.1, U6.23 (FB)
unnamed: R17.1, U6.26 (PWR)
unnamed: R19.1, U9.5 (OUT)
unnamed: R25.1, R26.2, U7.6 (PA0), U7.9 (PA3)
unnamed: R27.2, R28.1, U7.7 (PA1), U7.8 (PA2)
unnamed: R30.2, R31.1, U10.2 (FB)
VOUT: C32.1, D5.1 (K), Q2.3 (S), R15.2, R21.1, R26.1, R27.1, U6.1 (OUT); also elsewhere on the board

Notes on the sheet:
Emergency Stop
open-drain
USART2
PB9 = BOOT0 low = run from flash
TODO: gate TVS?
52.5 V - 55.4 V overvoltage lockout hysteresis
16.1 V - 18.9 V nominal undervoltage lockout hysteresis
Using 4m Rsns, current limit trips at 12.5 amps (nominal)
VIN divider 2.17V @48V Trigger when VOUT > 50.2V (Without tolerances)
I2C1
COMP1 on PA0/PA1 COMP2 on PA3/PA2
printf()
18.9 V threshold Power Good
Schottky diode to eat kickback energy at power-off
Misc MCU Debris
I2C addr: ZZZ = 0x40
TODO: verify Rpwr isn't too low
dV/dt startup method for LM5066
SS floating = 4ms rise time
RT floating = 500 kHz
ARM Cortex-M SWD
20 uA / C27 = 0.133 V / ms ramp rate
soft-start ramp time = 2.3ms

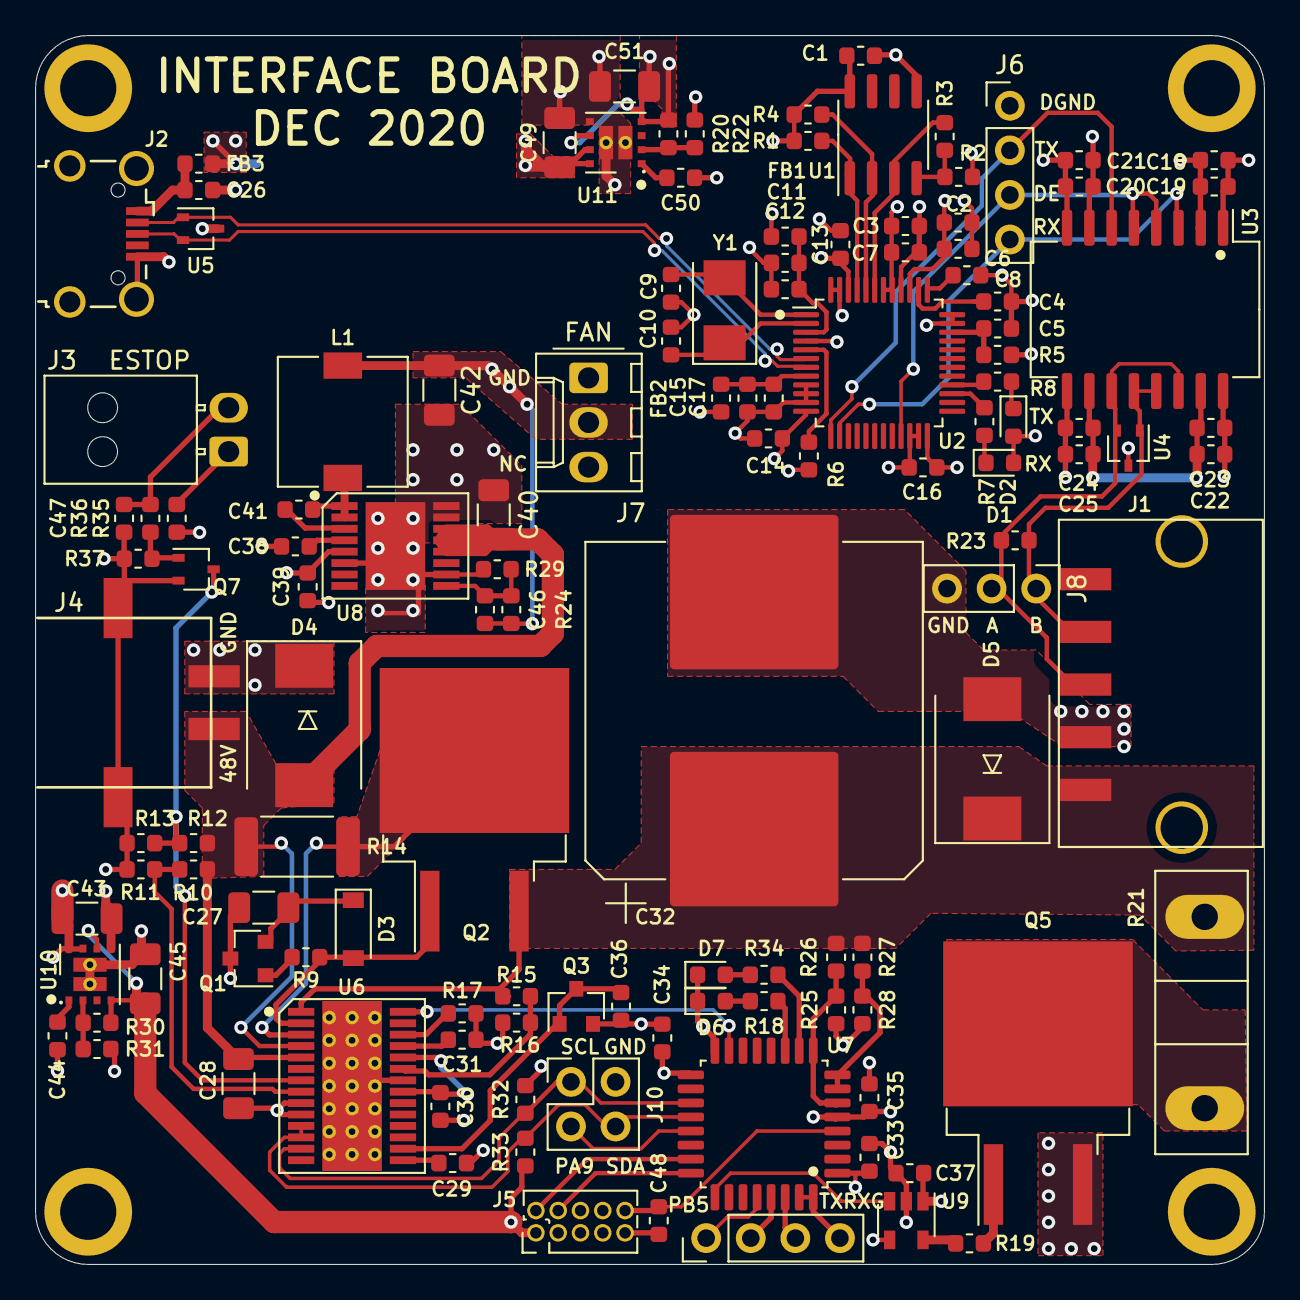
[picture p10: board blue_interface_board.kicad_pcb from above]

Board: 4 copper layers, 70.0 x 70.0 mm, 130 parts (0 on the bottom side), 77 nets.

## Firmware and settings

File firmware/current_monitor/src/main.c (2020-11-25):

/**
 * Primary executable for the current monitor chip.
 */

#include "stdint.h"
#include "stdlib.h"

#include "hw.h"
#include "stm32l0xx_hal.h"
#include "stm32l0xx_hal_gpio.h"
#include "stm32l0xx_hal_rcc.h"
#include "stm32l0xx_hal_tim.h"


/* Private function prototypes -----------------------------------------------*/
static void SystemClock_Config(void);
static void GPIO_Config(void);
static void TIM_Config(void);

static GPIO_InitTypeDef GPIO_InitStruct;
static GPIO_InitTypeDef SHUNT_PIN_InitStruct;
static TIM_HandleTypeDef TIM_InitStruct;
static TIM_OC_InitTypeDef sConfig;


int main(void) {
  HAL_Init();

  // Initialize the system clock.
  SystemClock_Config();

  // Configure the GPIO pins.
  GPIO_Config();

  // Configure Timers.
  TIM_Config();

  while (1) {
    HAL_GPIO_TogglePin(LED_PORT, GREEN_LED_PIN);
    HAL_Delay(100);
    HAL_GPIO_TogglePin(LED_PORT, RED_LED_PIN);
  }

  return 1;
}

void GPIO_Config() {

  // Enable the GPIO Clock.
  __HAL_RCC_GPIOA_CLK_ENABLE();
  __HAL_RCC_GPIOC_CLK_ENABLE();

  GPIO_InitStruct.Mode  = GPIO_MODE_OUTPUT_PP;
  GPIO_InitStruct.Pull  = GPIO_NOPULL;
  GPIO_InitStruct.Speed = GPIO_SPEED_FREQ_VERY_HIGH;
  GPIO_InitStruct.Pin = GREEN_LED_PIN | RED_LED_PIN;
  HAL_GPIO_Init(LED_PORT, &GPIO_InitStruct);

  GPIO_InitStruct.Pull = GPIO_NOPULL;
  GPIO_InitStruct.Pin  = GPIO_PIN_15;
  HAL_GPIO_Init(GPIOC, &GPIO_InitStruct);

  // Configure the PWM Pin.
  SHUNT_PIN_InitStruct.Mode = GPIO_MODE_AF_PP;
  SHUNT_PIN_InitStruct.Pull = GPIO_NOPULL;
  SHUNT_PIN_InitStruct.Speed = GPIO_SPEED_FREQ_LOW;
  SHUNT_PIN_InitStruct.Pin = SHUNT_EN_PIN;
  SHUNT_PIN_InitStruct.Alternate = GPIO_AF5_TIM2;
  HAL_GPIO_Init(SHUNT_EN_PORT, &SHUNT_PIN_InitStruct);
}

/**
 * Configuring TIM2 Channel 1 to run PWM at 1kHz.
 **/
void TIM_Config() {
  __HAL_RCC_TIM2_CLK_ENABLE();

  TIM_InitStruct.Instance = TIM2;

  uint32_t period = (uint32_t)(SystemCoreClock / 1000) - 1;
  /* Clock prescaler is 1. Count on every clock tick. */
  TIM_InitStruct.Init.Prescaler = 0;
  TIM_InitStruct.Init.CounterMode = TIM_COUNTERMODE_UP;
  /* Reset whenever the count reaches the value that equates to the desired
   * frequency as a fraction of the clock frequency. */
  TIM_InitStruct.Init.Period = period;
  /* Don't divide the clock. */
  TIM_InitStruct.Init.ClockDivision = TIM_CLOCKDIVISION_DIV1;
  /* Reset the counter to 0. */
  TIM_InitStruct.Init.AutoReloadPreload = 0;

  TIM_InitStruct.Channel = TIM_CHANNEL_1;

  if (HAL_TIM_PWM_Init(&TIM_InitStruct) != HAL_OK) {
    while(1);
  }

  sConfig.OCMode       = TIM_OCMODE_PWM1;
  sConfig.OCPolarity   = TIM_OCPOLARITY_HIGH;
  sConfig.OCFastMode   = TIM_OCFAST_DISABLE;

  /* Set the pulse value for channel 1 to 50% duty cycle */
  sConfig.Pulse = period * 0.25;
  if (HAL_TIM_PWM_ConfigChannel(&TIM_InitStruct, &sConfig, TIM_CHANNEL_1) != HAL_OK) {
    while(1);
  }
  if (HAL_TIM_PWM_Start(&TIM_InitStruct, TIM_CHANNEL_1) != HAL_OK) {
    while(1);
  }
}

/**
  * @brief  System Clock Configuration
  *         The system Clock is configured as follow : 
  *            System Clock source            = HSI
  *            SYSCLK(Hz)                     = 16000000
  *            HCLK(Hz)                       = 16000000
  *            AHB Prescaler                  = 1
  *            APB1 Prescaler                 = 1
  *            APB2 Prescaler                 = 1
  *            Flash Latency(WS)              = 0
  *            Main regulator output voltage  = Scale3 mode
  * @retval None
  */
void SystemClock_Config(void)
{
  RCC_ClkInitTypeDef RCC_ClkInitStruct = {0};
  RCC_OscInitTypeDef RCC_OscInitStruct = {0};
  
  /* Enable HSI Oscillator */
  RCC_OscInitStruct.OscillatorType = RCC_OSCILLATORTYPE_HSI;
  RCC_OscInitStruct.HSIState = RCC_HSI_ON;
  RCC_OscInitStruct.HSICalibrationValue = 1;
  RCC_OscInitStruct.MSIState = RCC_MSI_OFF;
  RCC_OscInitStruct.PLL.PLLState = RCC_PLL_NONE;
  if (HAL_RCC_OscConfig(&RCC_OscInitStruct)!= HAL_OK)
  {
    /* Initialization Error */
    while(1); 
  }
  
  /* Select HSI as system clock source and configure the HCLK, PCLK1 and PCLK2 
     clocks dividers */
  RCC_ClkInitStruct.ClockType = (RCC_CLOCKTYPE_SYSCLK | RCC_CLOCKTYPE_HCLK | RCC_CLOCKTYPE_PCLK1 | RCC_CLOCKTYPE_PCLK2);
  RCC_ClkInitStruct.SYSCLKSource = RCC_SYSCLKSOURCE_HSI;
  RCC_ClkInitStruct.AHBCLKDivider = RCC_SYSCLK_DIV1;
  RCC_ClkInitStruct.APB1CLKDivider = RCC_HCLK_DIV1;  
  RCC_ClkInitStruct.APB2CLKDivider = RCC_HCLK_DIV1;  
  if (HAL_RCC_ClockConfig(&RCC_ClkInitStruct, FLASH_LATENCY_0)!= HAL_OK)
  {
    /* Initialization Error */
    while(1); 
  }
}

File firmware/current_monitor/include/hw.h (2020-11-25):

/**
 * Human readable representations of Hardware.
 */

#define LED_PORT GPIOA
#define GREEN_LED_PIN GPIO_PIN_4
#define RED_LED_PIN GPIO_PIN_5

#define SHUNT_EN_PIN   GPIO_PIN_15
#define SHUNT_EN_PORT  GPIOA

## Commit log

2019-07-11 First draft of schematic for interface board
    Includes following features:
    * Hotswap controller with TVS diodes for control of input spikes
    * Fully isolated RS485 driver (also protected by TVS diodes on the data lines)
    * USB high speed FTDI USB - RS485 controller, capable of bauds up to 12 MBps
    [Comms.sch, Power.sch, blue_interface_board.kicad_pcb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]
2019-07-12 Added protection from motor regeneration through capacitors + MOSFET, started placement and routing
    [Comms.sch, Power.sch, blue_interface_board.kicad_pcb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]
2019-07-19 WIP with component placement
    [Comms.sch, Power.sch, blue_interface_board.kicad_pcb]
2019-08-06 Finished schematic, placement and routing, only silkscreen TODO
    [Comms.sch, Power.sch, blue_interface_board.kicad_pcb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]
2019-08-28 Fixed flipped connector, changed most placement
    [Comms.sch, Power.sch, blue_interface_board.kicad_pcb]
2019-11-18 Fix DRCs and minor improvements
    [Comms.sch, Power.sch, blue_interface_board.kicad_pcb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]
2019-11-18 Silk screen and cosmetic fixes
    [Power.sch, blue_interface_board.kicad_pcb]
2019-11-19 Changed voltage regulator, added I2C interface
    [Comms.sch, Power.sch, blue_interface_board.kicad_pcb]
2019-12-05 Changed connectors to microfit, added fan output
    [Comms.sch, Power.sch, blue_interface_board.kicad_pcb]
2019-12-05 Fixed power limit to avoid going into fault
    [Power.sch]
2019-12-10 Reverted to nanofit for e-stop
    [Power.sch, blue_interface_board.kicad_pcb]
2019-12-11 Changed USB connector to be on same side
    [blue_interface_board.kicad_pcb, blue_interface_board.sch]
2020-02-18 add rs485 termination, change to SOT-323 TVS diodes, various OCD
    [Comms.sch, Power.sch, blue_interface_board.kicad_pcb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]
2020-02-19 working through the power subsystems now. changed e-stop topology.
    [Comms.sch, Power.sch, blue_interface_board.kicad_pcb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]
2020-02-21 adding a few notes
    [Power.sch]
2020-02-22 add two part numbers
    [Comms.sch, Power.sch]
2020-02-22 recalculate lm5066 passives
    [Power.sch, blue_interface_board.kicad_pcb]
2020-02-22 fix Q3 pinout and chase a few part numbers
    [Power.sch, blue_interface_board.kicad_pcb]
2020-02-24 WIP 48v-12v dc/dc converter tweaks. need to restore to BLDC values
    [Power.sch, blue_interface_board.kicad_pcb]
2020-02-24 add MCU reset cap, tweak dc-dc feedback divider
    [Power.sch, blue_interface_board.kicad_pcb]
2020-02-25 add part numbers, minor tweaks
    [Power.sch, blue_interface_board.kicad_pcb]
2020-02-25 add MOSFET drive IC, simply a bit by pushing more into MCU, tweak layout
    [Power.sch, blue_interface_board.kicad_pcb]
2020-02-25 Adding motor capacitive load
2020-02-25 layout tweaks. add debugging headers.
    [Power.sch, blue_interface_board.kicad_pcb]
2020-02-26 ready to generate CAM
    [Comms.sch, Power.sch, blue_interface_board.kicad_pcb]
2020-02-26 CAM generation for rev A1 fab order
    [blue_interface_board-B_Cu.gbr, blue_interface_board-B_Mask.gbr, blue_interface_board-B_Paste.gbr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]
2020-02-26 commit schematics for convenience when writing firmware
2020-02-27 repo restructuring, readme, and a tiny bit of documentation
    [Comms.sch, Power.sch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]
2020-09-06 Updating to new files and minor resistor fix
    [Comms.kicad_sch, Power.kicad_sch, blue_interface_board.kicad_pcb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]
2020-09-06 Regen with resistor update
    [bom.csv]
2020-11-03 Power Bump to 530W+ (#3)
    * Rsns to 5m (13A limit)
    * Adding resistors for external divider (allows higher current sense)
    * Adjusting timeout capacitor (1uF -> 52ms)
    * Adjusting feedback resistors.
    * Adding ERD resistors to layout.
    * Revert "Adjusting timeout capacitor (1uF -> 52ms)"
    This reverts commit 7a30909a9925d87866bd3a766fa9658db1f002d2.
    * Removing external resistor divider.
    * Bumping Rpwr
    * Adjusting Timer (C31)
    * Updating info from schematic
    * Adding second Power FET
    * Revert "Adding second Power FET"
    This reverts commit e632f1e0367ea6556d8bc6e08f99c25e5b9f6e16.
    [Comms.kicad_sch, Power.kicad_sch, blue_interface_board.kicad_pcb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]
2020-11-03 Updating BOM
    [bom.csv]
2020-11-11 Initial Controller Firmware (#4)
    * Adding STMCube submodule
    * Initial work for power controller
2020-11-20 12V rail supplied off of VIN and Shunt EN switched to a clockable pin.
    [Comms.kicad_sch, Power.kicad_sch, blue_interface_board.kicad_pcb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]
2020-11-20 Upload Debug (#6)
    * Add openocd config file
    * Progress continued
    * More make testing
    * More testing
    * Blink LED
    * makefile target for flashing via Olimex adapter
    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
2020-11-20 Initial work towards configuring Shunt PWM
2020-11-25 Demo that the shunt enable works with just pin toggles
2020-11-25 Clock Prescaler should be 0 otherwise every other tick skipped.
    [main.c]
2020-12-02 Updating all fab files
    [blue_interface_board-B_Cu.gbr, blue_interface_board-B_Mask.gbr, blue_interface_board-B_Paste.gbr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]
2020-12-02 Fixing PCB edges
    [blue_interface_board.kicad_pcb]
2020-12-05 Updating date
    [blue_interface_board-B_Cu.gbr, blue_interface_board-B_Mask.gbr, blue_interface_board-B_Paste.gbr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]
2020-12-15 Fix component sizing mistake (0402 -> 0603)
    [Comms.kicad_sch, Power.kicad_sch, bom.csv]
